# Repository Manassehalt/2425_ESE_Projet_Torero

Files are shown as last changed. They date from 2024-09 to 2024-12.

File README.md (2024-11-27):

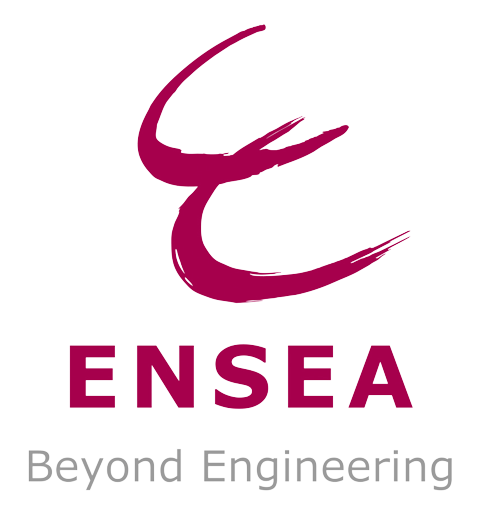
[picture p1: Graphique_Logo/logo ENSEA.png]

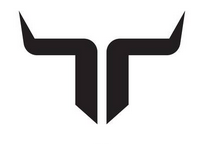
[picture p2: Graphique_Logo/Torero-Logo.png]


# 2425_ESE_Projet_Torero

## Projet de ESE de 3éme année de JACQUOT Nolan, GUIFFAULT Gabriel, BOULOT Paul et THOMAR Jean-Philippe

Ce projet contient toute les ressources de l'élaboration d'un robot capable de jouer au chat et a la souris.
Les liens vers les differentes ressources sont énuméré avec un court intitulé a la FIN du README.
Ci dessous le schéma architectural donnant les grandes lignes du projet.
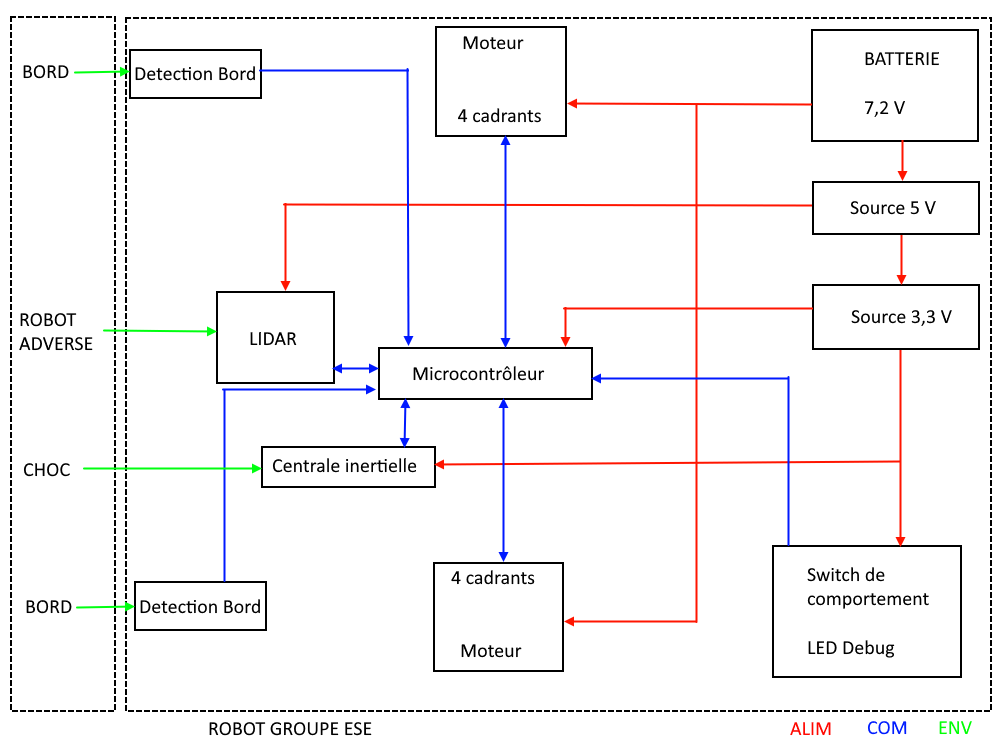
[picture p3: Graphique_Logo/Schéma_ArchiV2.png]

[Schéma architectural](https://github.com/user-attachments/files/17220902/Schema.architectural.pdf)

## Environnement:

> [!IMPORTANT]
> Table de 200cm x 160cm
> 
> Table sans Bord ni marquages!
> 
> Robot assimilable a un cylindre de 17 cm de diametre et 15 cm de hauteur 

## Cahier des charges:
> [!IMPORTANT]
>- Le robot doit etre capable de ce déplacer sur une table sans tomber (absence de bord et de marquage)
>- Le robot doit etre capable de detecter l'autre robot present sur la table pour le fuir ou le chasser en fonction de son role dans la partie.
>- Le robot doit etre capable de detecter un contact meme leger avec le robot adverse et changer son comportement d'un role vers l'autre.

Objectif annexe:
- Le robot peut realiser une odometrie simple pour suivre le bord de table lorsqu'il debute en souris
- Le robot peut realiser une odometrie simple pour se positionner au centre de la table avant de commencer la traque lorsqu'il debute en chat
- Le robot peut declencher un brusque changement de direction si il detecte un robot approchant rapidement en mode souris
- Le robot peut effectuer des prédiction de trajectoire et effectuer des trajectoires de collision en prévision du deplacement adverse en mode chat
- Le robot evite de prendre des directions ou il serait acculé dans un angle de table

### Dossier contenant les Datasheets : 
https://github.com/Manassehalt/2425_ESE_Projet_Torero/tree/main/Datasheet

### LISTE des choses faite ou a faire : 
https://github.com/Manassehalt/2425_ESE_Projet_Torero/blob/main/Calculs%20et%20brouillons/Remarque_Sch.md

### Lien utile : 
https://github.com/Manassehalt/2425_ESE_Projet_Torero/blob/main/Calculs%20et%20brouillons/Liens.xlsx

### BOM : 
https://github.com/Manassehalt/2425_ESE_Projet_Torero/blob/main/BOM.xlsx

### INFO PCB : 
https://github.com/Manassehalt/2425_ESE_Projet_Torero/blob/main/PCB/info_PCB.docx

### Apercu serigraphie :
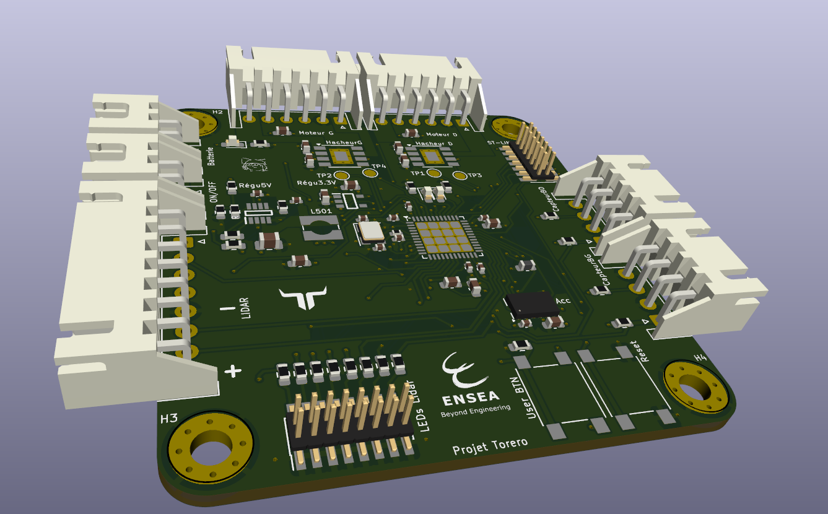
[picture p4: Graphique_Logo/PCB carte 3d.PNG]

[view PCB 3D](https://github.com/Manassehalt/2425_ESE_Projet_Torero/blob/main/Graphique_Logo/PCB%20carte%203d.PNG)

### DOSSIER PCB : 
https://github.com/Manassehalt/2425_ESE_Projet_Torero/tree/main/PCB

### Shematics_torero : 
https://github.com/Manassehalt/2425_ESE_Projet_Torero/blob/main/PCB/Projet_torero/Projet_torero.kicad_sch

### DOSSIER CODE STM32 : 
https://github.com/Manassehalt/2425_ESE_Projet_Torero/tree/main/Projet_ESE_STM32/Projet_ESE_Torero/STM32G431CBU6

### DOSSIER CALCULS : 
https://github.com/Manassehalt/2425_ESE_Projet_Torero/tree/8892ed05e16a1e8a040fe9dc08f9f57ab23dc9e8/Calculs%20et%20brouillons

### Methode si nouvel ordinateur : 
> [!TIP]
>Générer une clé SSH
>- Taper ssh-keygen puis Entrer
>- Appuyer sur y pour overwrite et sur Entrer pour passer les étapes (if no passphrase)
>- Taper cat ~/.ssh/id_ed25519.pub puis Entrer
>- Copier puis coller la clé dans GitHub Setting > SSH and GPG keys > SSH keys
>- Renommer avec le nom du PC pour savoir à quoi la clé correpond
>  ex : jeanp@HP-Pavilion-JP

### Ligne pour cloner un répertoire en utilisant le port 443 (https) au lieu du port 22, si bug sur la connexion:
> [!TIP]
>git clone ssh://git@ssh.github.com:443/username/Repositority_name.git

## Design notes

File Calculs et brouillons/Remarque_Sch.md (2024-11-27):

# !! LISTE A FAIRE !!
<details open>
<summary> <strong><ins>Schema:</ins></strong> </summary>
	
- [x] Regarder pour encodeurs 
- [x] Reprendre régulateur 5V (entrée à gauche et sortie à droite) 
- [x] VDDA pas alimenté 
- [x] Calculer valeur R pour les leds d'état 
- [x] supprimer label hiérarchique 7.2V 
- [x] Merge les feuilles pour moteur afin de modifier les deux à la fois 
- [x] faire symbole tof 
- [x] remplir valeur composants 
- [x] Renommer comme il faut pins de communication accélero 
- [x] Remplir le readme avec les schémas + calculs + présentation globale (ne pas avoir à aller chercher les fichiers à gauche à droite)
- [ ] Mettre texte descriptif pour définir connections
- [x] valeur R 2k3 plutôt que 2.3k  
- [x] valeur C 100n plutôt que 0.1µF  
- [x] Rendre l'ensemble plus clair (label et autre) 
</details>

<details >
<summary>  <strong><ins> PCB :</ins></strong> </summary>

- [x] PCB 54mm x 57mm
- [x] 4 trou de fixation a 4mm du bord Taille M3 
- [x] Remplacer l'empreinte de l'interrupteur pour le deporter hors du PCB 
- [x] condo proche 
- [x] reverifier empreinte condo imperial 
- [x] mettre port ldidar a coté de l'alimentation 5V
- [x] orientation serio j201 
- [x] en dernier les gpio pour le routage
- [x] router en premier les signaux rapides comme oscillateur, puis connecteur j201
- [x] plan de masse unique ideal
- [x] plan alim en 3,3V
- [x] changer empreinte grosse bobine 
- [x] 7.2V refaire connection (pas le meme tag) 
- [x] interrupteur a refaire empeinte plus petite 
- [x] refaire alim en suivant doc conseillé / 3 via 
- [x] Inverser pin driver moteur +zone de connexion plutot que piste 
- [x] rapprocher pastilles de ground et alim des vias associé 
- [x] aligner les composants 
- [x] Rapprocher la partie puissance (driver moteur) 
- [x] regarder plan pour retirer les antennes 
- [x] découplage 
- [x] plan sur grosse bobine 
- [x] agrandir piste gros courant 
  Routage :
- [x] Changement règle du CI -> diamètre mini via 0.45
		       -> diamètre mini anneaux 0.075
		       -> voir avec prof pour confirmer modifs (via copié depuis   correction fiack)
- [x] TESTER LES CONNECTIONS
      
</details open> 

<details >
<summary> <strong> <ins> MECANIQUE: </ins></strong></summary>

- [x] designer le parchoc qui porte les capteur de bord 
- [x] designer les support ajustable
- [ ] imprimer les pieces du robot

</details>
<details >
<summary>  <strong><ins> SOFTWARE: </ins></strong></summary>

- [ ] piloter les driver moteurs
- [ ] piloter le lidar
- [ ] recevoir les donnés du lidar et les interpréter
- [x] recevoir les donnés de l'accelerometre
- [ ] recevoir les donnés des capteurs de bords
- [ ] realiser les comportement en odometrie
- [ ] coder les comportement de fuite/evitement
- [ ] coder les comportement de chasse/collision
</details>

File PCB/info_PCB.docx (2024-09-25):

Batterie :

- Broche 1 = +
- Broche 2 = -

Switch à mettre sur un connecteur car PCB directement sous Lidar

57mm/54mm

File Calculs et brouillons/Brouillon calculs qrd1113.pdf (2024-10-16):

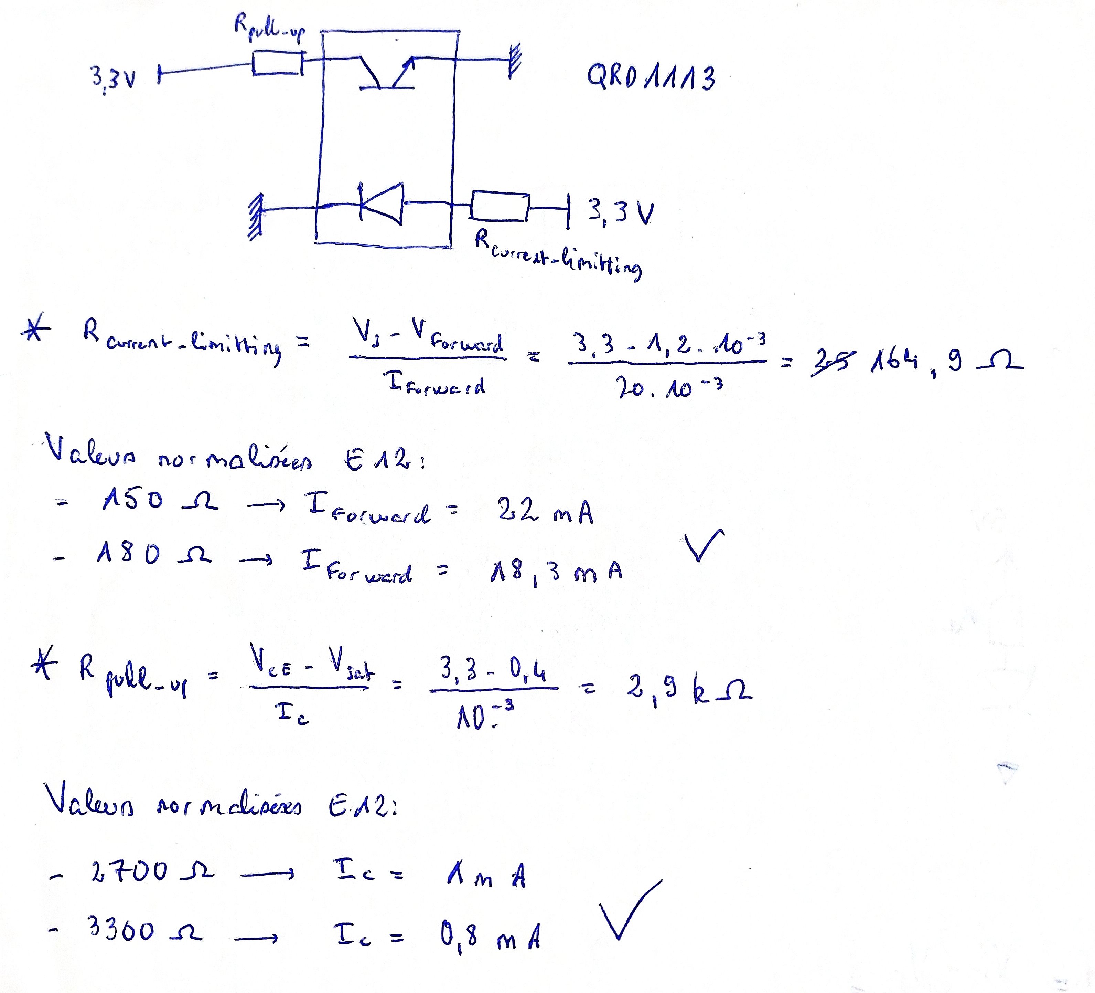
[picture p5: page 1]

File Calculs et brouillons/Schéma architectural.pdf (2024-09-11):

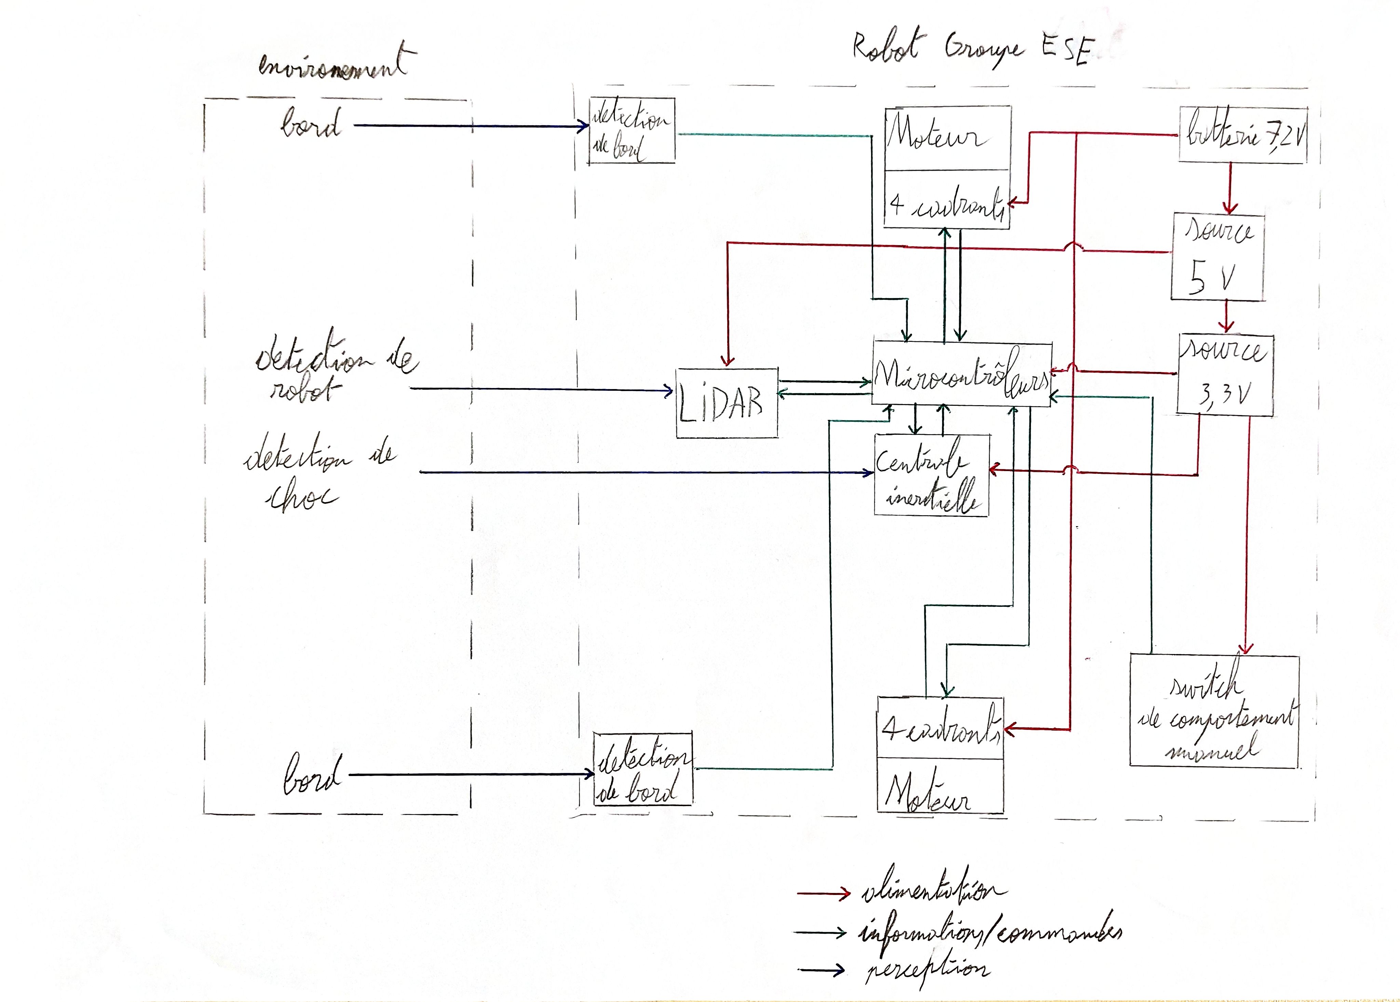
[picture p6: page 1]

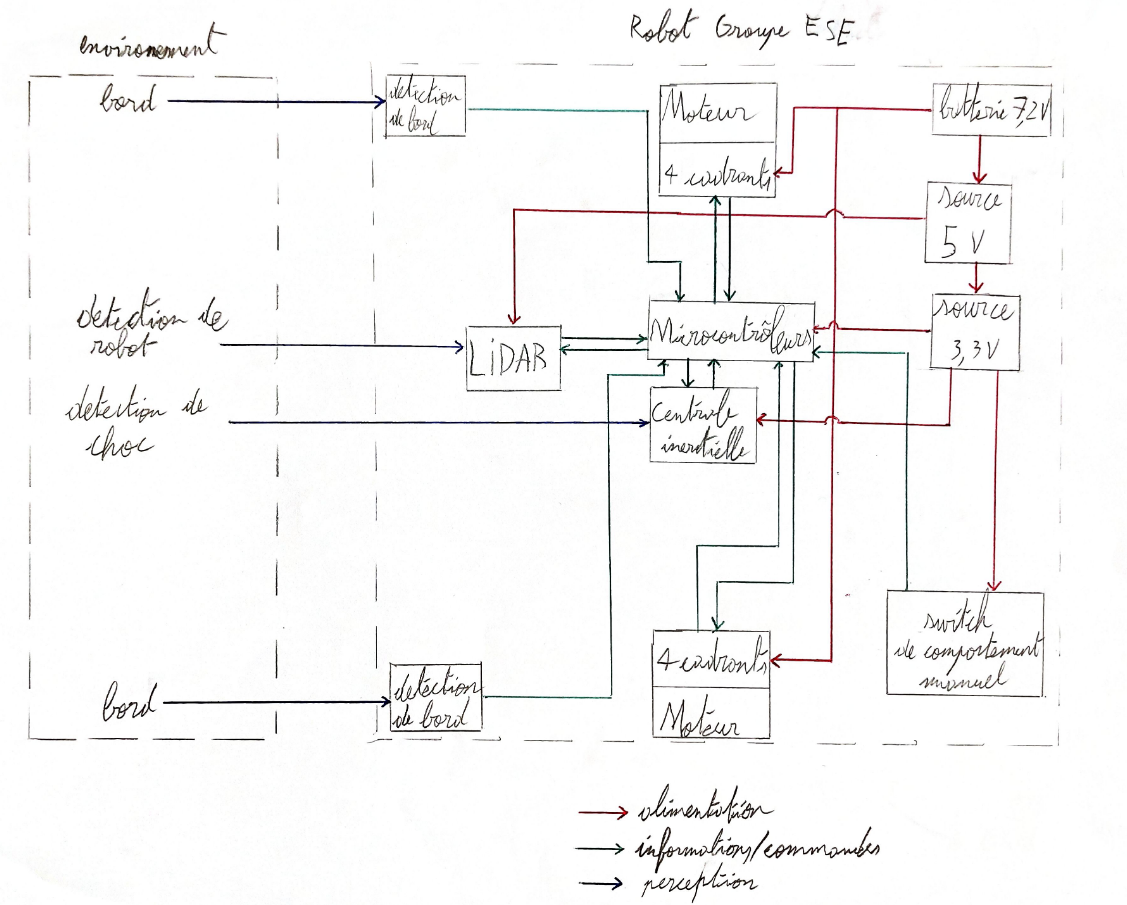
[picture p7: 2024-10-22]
Graphique_Logo/Schema_archi.png

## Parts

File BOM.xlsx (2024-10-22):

NOM | REFERENCE | FOURNISSEUR | DESCRIPTION | PRIX UNITAIRE | QUANTITE | COUT TOTAL | STATUS COMMANDE | DATASHEET
STM32G431CBU6 |  |  | Microcontrôleur |  | 1 | 0.00 €
Quartz 16 MHz | 2853935 | Farnell |  |  | 1 | 0.00 €
Connecteur SWD/STLink | 3226055 | Farnell |  |  |  | 0.00 €
ZXBM5210-SP-13 |  |  | Driver moteur |  |  | 0.00 €
DfRobot FIT0520 ou FIT0521 |  |  | Moteurs |  | 2 | 0.00 €
ADXL343BCCZ-RL |  |  | Accéléromètre |  | 1 | 0.00 €
MP1475S |  |  | Régulateur 5V |  | 1 | 0.00 €
BU33SD5WG-TR |  |  | Régulateur 3.3V |  | 1 | 0.00 €
NIMH 7.2V 1.3Ah (RS : 777-0377) |  |  | Batterie 7.2V |  |  | 0.00 €
QRD1113 | 1467857/1467858 | Farnell | Capteur bordure |  | 2 | 0.00 €
YDLIDAR X4 |  |  | Lidar |  | 1 | 0.00 €
Connecteurs JST 2.54mm |  |  |  |  |  | 0.00 €
LED + R/C |  |  |  |  |  | 0.00 € | en 0603
Résistance 10 k |  |  | Résistance boot flash user button |  | 1
Capacité 20p |  |  |  |  | 2
Capacité 100n |  |  |  |  | 8
Capacité 1u |  |  |  |  | 9
Capacité 4n7 |  |  |  |  | 1
Capacité 10n |  |  |  |  | 1
Capacité 22u |  |  |  |  | 1
Capacité 47u |  |  |  |  | 1
Capacité 10u |  |  |  |  | 2
Diode rouge |  |  |  |  | 2
Diode verte |  |  |  |  | 1
Connecteur Pin header 2x7 1,27mm ST Link |  |  |  |  | 1
Connecteur Pin header 2x8 1,27mm debug Lidar |  |  |  |  | 1
Connecteur JST 1x8 2,5mm Lidar |  |  |  |  | 1
Connecteurs JST 1x 2 2,5mm (batterie + switch) |  |  |  |  | 2
Connecteur JST 1x6 2,5mm moteur |  |  |  |  | 2
Inductance passe bas VDDA stm32 |  |  |  |  | 1
Inductance 4u7 |  |  | Régulateur tension 5V |  | 1
Résistance 10 |  |  |  |  | 1
Résistance 120 |  |  |  |  | 1
Résistance 140 |  |  |  |  | 2
Résistance 1k |  |  |  |  | 8
Résistance 100k |  |  |  |  | 2
Résistance 20 |  |  |  |  | 1
Résistance 16k |  |  |  |  | 1
Résistance 40k2 |  |  |  |  | 1
Résistance 7k68 |  |  |  |  | 1
Résistance 300 |  |  |  |  | 2
Résistance 15k3 |  |  |  |  | 2
Switch push |  |  | stm32 NRST et Boot Flash |  | 2

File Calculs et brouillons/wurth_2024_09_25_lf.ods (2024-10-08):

Value | Footprint | Tension | Qty | Wuerth
100nF | 402 | 25 | 1000 | 885012205085
15pF | 402 | 50 | 100 | 885012005056
10pF | 402 | 50 | 1000 | 885012005055
1uF | 603 | 25 | 1000 | 885012206076
10nF | 402 | 50 | 1000 | 885012205067
4.7uF | 603 | 10 | 1000 | 885012106012
22uF | 805 | 25 | 1000 | 885012107019
10uF | 603 | 25 | 1000 | 885012106031
6.8uH | >2A |  | 100 | 74404054068
4.7uH | >2A |  | 100 | 74404052047

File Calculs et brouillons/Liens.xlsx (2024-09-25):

DESCRIPTION | LIENS
Guide pour les calculs et branchement du capteur de bord QRD1113/14(attention arduino) | https://learn.sparkfun.com/tutorials/qrd1114-optical-detector-hookup-guide/all
Current Limiting Resistor: Protective Resistor for Regulating Current (for QRD1113/14) | https://www.ourpcb.com/current-limiting-resistor.html

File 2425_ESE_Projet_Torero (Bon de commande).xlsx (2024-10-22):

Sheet: Farnell
Farnell |  |  |  |  | Envoyez un seul fichier par mail!
Pos | I | P | Art | Désignation | Qté commandée | UA | Date Livraison | Prix unitaire | Devise | Q | Grpe | Div
10 | Z |  |  | 1467857 Capteur bordure QRD1113 | 4 | PC |  | 2.09 | EUR | PC | TA.01
20 | Z |  |  |  |  | PC |  |  | EUR | PC | TA.01
30 | Z |  |  |  |  | PC |  |  | EUR | PC | TA.01
40 | Z |  |  |  |  | PC |  |  | EUR | PC | TA.01
50 | Z |  |  |  |  | PC |  |  | EUR | PC | TA.01
60 | Z |  |  |  |  | PC |  |  | EUR | PC | TA.01
70 | Z |  |  |  |  | PC |  |  | EUR | PC | TA.01
80 | Z |  |  |  |  | PC |  |  | EUR | PC | TA.01
90 | Z |  |  |  |  | PC |  |  | EUR | PC | TA.01
100 | Z |  |  |  |  | PC |  |  | EUR | PC | TA.01
110 | Z |  |  |  |  | PC |  |  | EUR | PC | TA.01
120 | Z |  |  |  |  | PC |  |  | EUR | PC | TA.01
130 | Z |  |  |  |  | PC |  |  | EUR | PC | TA.01
140 | Z |  |  |  |  | PC |  |  | EUR | PC | TA.01
150 | Z |  |  |  |  | PC |  |  | EUR | PC | TA.01
160 | Z |  |  |  |  | PC |  |  | EUR | PC | TA.01
170 | Z |  |  |  |  | PC |  |  | EUR | PC | TA.01
180 | Z |  |  |  |  | PC |  |  | EUR | PC | TA.01
190 | Z |  |  |  |  | PC |  |  | EUR | PC | TA.01
MODE d'EMPLOI et CODE erreurs Version 19
1: indiquez le fournisseur ligne 1
2:remplissez pour chaque ligne commandée les 4 champs en rouge selon les règles suivantes:
 | Art
 |  |  | 2.1 | Ne mettez rien ici tout comme dans P: remplissez les zones rouges (et pas ailleurs)
 | Désignation
 |  |  | 2.2 | Ne dépassez pas les 40 caractères: il seront automatiquement effacés lors de la recopie
 |  |  | 2.3 | Mettre le code commande impérativement en premier suivi d'une courte description
 |  |  | 2.4 | Pour RS et Farnell : mettre le code commande RS ou Farnell (7 à 9 chiffres) (et pas la référence constructeur) suivie d'une courte description
 |  |  | 2.5 | Exemple: 125-4857 capa 1uF 0508
 | Qté commandée
 |  |  | 2.6 | C'est le nombre d'unités correspondant au prix unitaire
 |  |  | 2.7 | Attention il y a des pièges
 |  |  | 2.8 | avec RS par exemple on vous demande parfois de commander par lot de 5 par exemple
 |  |  | 2.9 | si vous commandez 1 lot : le nombre d'unité est alors 5 pour 1 lot et non 1
 | date
 |  |  | 2.10 | Pour la date: mettre la de date dans une semaine
 |  |  | 2.11 | La mettre au format JJ.MM.AAAA
 |  |  | 2.13 | Bien utiliser les points comme séparateur
 | prix unitaire
 |  |  | 2.14 | Le prix est le prix HT (sans la TVA 20%) en euros d'une unité | sauf pour les commandes au comptant ou chez un fournisseur étranger (EXP-TECH par exemple): mettez le prix TTC
 |  |  | 2.15 | arrondi au centime supérieur (0.012 euros devient 0.02!)
 |  |  | 2.16 | avec pour séparateur le point
 |  |  | 2.17 | n'utilisez pas le symbole euros d'excel
3: frais de port
 |  |  | 3.1 | ajoutez une ligne pour les frais de port
 |  |  | 3.2 | dont la désignation est "frais de port"
 |  |  | 3.3 | pas de frais de port à mettre pour RS ou Farnell
 |  |  | 3.4 | Renseignez vous pour connaître les frais de port | 9,9 euros TTC chez EXP par exemple
4: conseils complémentaires
 |  |  | 4.1 | Ne modifier que les 4 champs en rouge
 |  |  | 4.2 | Ne pas modifier le document sinon cela n'a plus aucun intérêt
 |  |  | 4.3 | Mettez les références dans le même ordre que celui de la commande
 |  |  | 4.4 | Vérifier bien sur les sites les références et les prix!
 |  |  | 4.5 | N'oubliez pas les frais de port!: ajoutez une ligne pour les mentionner
5: sauvegardez le fichier au format xls

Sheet: RS
RS |  |  |  |  | Envoyez un seul fichier par mail!
Pos | I | P | Art | Désignation | Qté commandée | UA | Date Livraison | Prix unitaire | Devise | Q | Grpe | Div
10 | Z |  |  | 820-1605 Connecteur JST 1x8 2,5mm | 5 | PC |  | 0.3 | EUR | PC | TA.01
20 | Z |  |  | 515-1349 connecteur JST 1x6 2,5mm | 10 | PC |  | 0.27 | EUR | PC | TA.01
30 | Z |  |  | 820-1582 connecteur JST 1x2 2,5mm | 5 | PC |  | 0.27 | EUR | PC | TA.01
40 | Z |  |  | 479-1435 switch push button 6 x 6 x 9.5mm | 20 | PC |  | 0.15 | EUR | PC | TA.01
50 | Z |  |  | 828-1866 connecteur pin header 2x8 1,27mm | 5 | PC |  | 2.05 | EUR | PC | TA.01
60 | Z |  |  | 828-1862 connecteur pin header 2x7 1,27mm | 5 | PC |  | 1.54 | EUR | PC | TA.01
70 | Z |  |  |  |  | PC |  |  | EUR | PC | TA.01
80 | Z |  |  |  |  | PC |  |  | EUR | PC | TA.01
90 | Z |  |  |  |  | PC |  |  | EUR | PC | TA.01
100 | Z |  |  |  |  | PC |  |  | EUR | PC | TA.01
110 | Z |  |  |  |  | PC |  |  | EUR | PC | TA.01
120 | Z |  |  |  |  | PC |  |  | EUR | PC | TA.01
130 | Z |  |  |  |  | PC |  |  | EUR | PC | TA.01
140 | Z |  |  |  |  | PC |  |  | EUR | PC | TA.01
150 | Z |  |  |  |  | PC |  |  | EUR | PC | TA.01
160 | Z |  |  |  |  | PC |  |  | EUR | PC | TA.01
170 | Z |  |  |  |  | PC |  |  | EUR | PC | TA.01
180 | Z |  |  |  |  | PC |  |  | EUR | PC | TA.01
190 | Z |  |  |  |  | PC |  |  | EUR | PC | TA.01
MODE d'EMPLOI et CODE erreurs Version 19
1: indiquez le fournisseur ligne 1
2:remplissez pour chaque ligne commandée les 4 champs en rouge selon les règles suivantes:
 | Art
 |  |  | 2.1 | Ne mettez rien ici tout comme dans P: remplissez les zones rouges (et pas ailleurs)
 | Désignation
 |  |  | 2.2 | Ne dépassez pas les 40 caractères: il seront automatiquement effacés lors de la recopie
 |  |  | 2.3 | Mettre le code commande impérativement en premier suivi d'une courte description
 |  |  | 2.4 | Pour RS et Farnell : mettre le code commande RS ou Farnell (7 à 9 chiffres) (et pas la référence constructeur) suivie d'une courte description
 |  |  | 2.5 | Exemple: 125-4857 capa 1uF 0508
 | Qté commandée
 |  |  | 2.6 | C'est le nombre d'unités correspondant au prix unitaire
 |  |  | 2.7 | Attention il y a des pièges
 |  |  | 2.8 | avec RS par exemple on vous demande parfois de commander par lot de 5 par exemple
 |  |  | 2.9 | si vous commandez 1 lot : le nombre d'unité est alors 5 pour 1 lot et non 1
 | date
 |  |  | 2.10 | Pour la date: mettre la de date dans une semaine
 |  |  | 2.11 | La mettre au format JJ.MM.AAAA
 |  |  | 2.13 | Bien utiliser les points comme séparateur
 | prix unitaire
 |  |  | 2.14 | Le prix est le prix HT (sans la TVA 20%) en euros d'une unité | sauf pour les commandes au comptant ou chez un fournisseur étranger (EXP-TECH par exemple): mettez le prix TTC
 |  |  | 2.15 | arrondi au centime supérieur (0.012 euros devient 0.02!)
 |  |  | 2.16 | avec pour séparateur le point
 |  |  | 2.17 | n'utilisez pas le symbole euros d'excel
3: frais de port
 |  |  | 3.1 | ajoutez une ligne pour les frais de port
 |  |  | 3.2 | dont la désignation est "frais de port"
 |  |  | 3.3 | pas de frais de port à mettre pour RS ou Farnell
 |  |  | 3.4 | Renseignez vous pour connaître les frais de port | 9,9 euros TTC chez EXP par exemple
4: conseils complémentaires
 |  |  | 4.1 | Ne modifier que les 4 champs en rouge
 |  |  | 4.2 | Ne pas modifier le document sinon cela n'a plus aucun intérêt
 |  |  | 4.3 | Mettez les références dans le même ordre que celui de la commande
 |  |  | 4.4 | Vérifier bien sur les sites les références et les prix!
 |  |  | 4.5 | N'oubliez pas les frais de port!: ajoutez une ligne pour les mentionner
5: sauvegardez le fichier au format xls

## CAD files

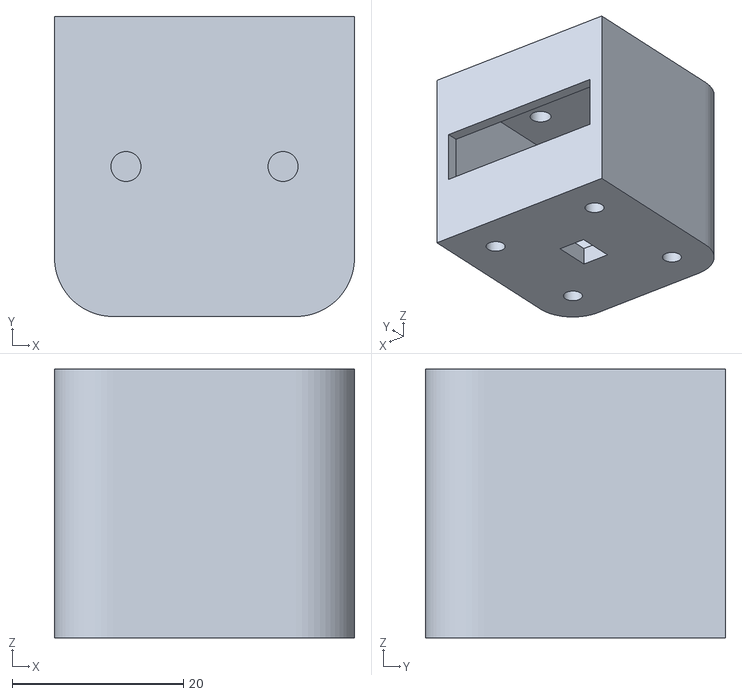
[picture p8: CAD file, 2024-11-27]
Meca/SupportCapteur.stl
35.0 x 35.0 x 31.4

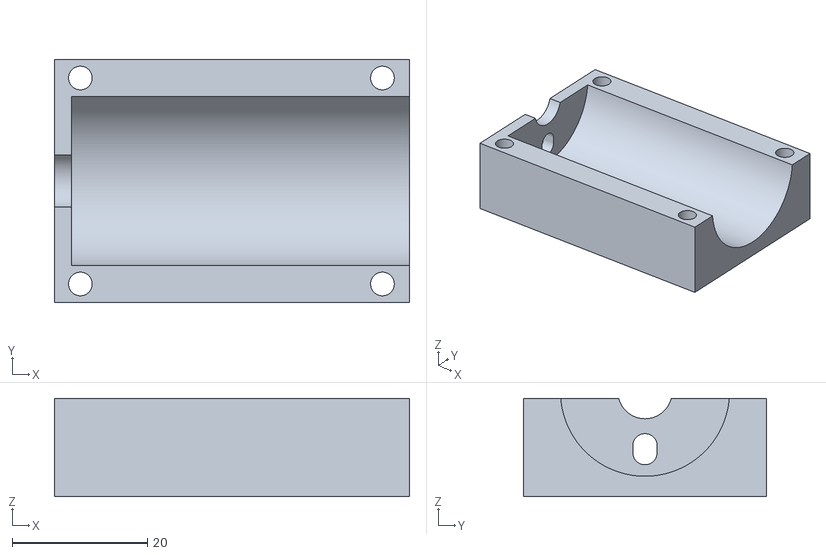
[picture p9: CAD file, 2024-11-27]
Meca/SupportMotor.stl
52.5 x 36.0 x 14.5

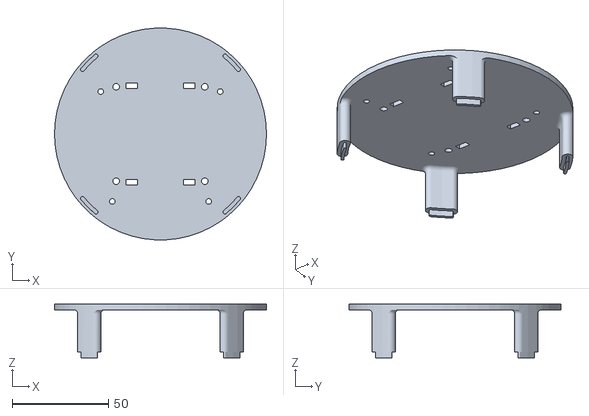
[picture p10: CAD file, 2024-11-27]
Meca/Tower.stl
110.0 x 109.8 x 28.0

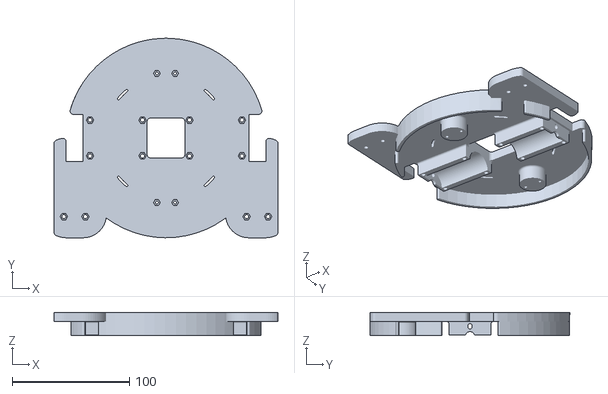
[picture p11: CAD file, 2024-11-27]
Meca/Base.stl
190.8 x 170.0 x 20.0

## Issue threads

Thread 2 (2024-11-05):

task list

gg-info, 2024-11-05:
# !! LISTE A FAIRE !!

- [x] Regarder pour encodeurs
- [x] Reprendre régulateur 5V (entrée à gauche et sortie à droite)
- [x] VDDA pas alimenté
- [x] Calculer valeur R pour les leds d'état
- [x] supprimer label hiérarchique 7.2V
- [x] Merge les feuilles pour moteur afin de modifier les deux à la fois
- [x] faire symbole tof
- [x] remplir valeur composants
- [x] Renommer comme il faut pins de communication accélero
- [x] Remplir le readme avec les schémas + calculs + présentation globale (ne pas avoir à aller chercher les fichiers à gauche à droite)
- [ ] Mettre texte descriptif pour définir connections
- [x] valeur R 2k3 plutôt que 2.3k
- [x] valeur C 100n plutôt que 0.1µF
- [x] Rendre l'ensemble plus clair (label et autre)

### Description du PCB :

- [x] PCB 54mm x 57mm
- [x] 4 trou de fixation a 4mm du bord Taille M3
- [x] Remplacer l'empreinte de l'interrupteur pour le deporter hors du PCB
- [x] condo proche
- [x] reverifier empreinte condo imperial
- [x] mettre port ldidar a coté de l'alimentation 5V
- [x] orientation serio j201
- [x] en dernier les gpio pour le routage
- [x] router en premier les signaux rapides comme oscillateur, puis connecteur j201
- [x] plan de masse unique ideal
- [x] plan alim en 3,3V
- [x] changer empreinte grosse bobine
- [x] 7.2V refaire connection (pas le meme tag)
- [x] interrupteur a refaire empeinte plus petite
- [x] refaire alim en suivant doc conseillé / 3 via
- [x] Inverser pin driver moteur +zone de connexion plutot que piste
- [x] rapprocher pastilles de ground et alim des vias associé
- [x] aligner les composants
- [x] Rapprocher la partie puissance (driver moteur)
- [x] regarder plan pour retirer les antennes
- [x] découplage
- [x] plan sur grosse bobine
- [x] agrandir piste gros courant
  Routage :
- [x] Changement règle du CI -> diamètre mini via 0.45
		       -> diamètre mini anneaux 0.075
		       -> voir avec prof pour confirmer modifs (via copié depuis   correction fiack)
- [ ] TESTER LES CONNECTIONS

### MECANIQUE:

- [ ] designer le parchoc qui porte les capteur de bord
- [ ] designer les support ajustable
- [ ] imprimer les pieces du robot

### SOFTWARE:

- [ ] piloter les driver moteurs
- [ ] piloter le lidar
- [ ] recevoir les donnés du lidar et les interpréter
- [ ] recevoir les donnés de l'accelerometre
- [ ] recevoir les donnés des capteurs de bords
- [ ] realiser les comportement en odometrie
- [ ] coder les comportement de fuite/evitement
- [ ] coder les comportement de chasse/collision

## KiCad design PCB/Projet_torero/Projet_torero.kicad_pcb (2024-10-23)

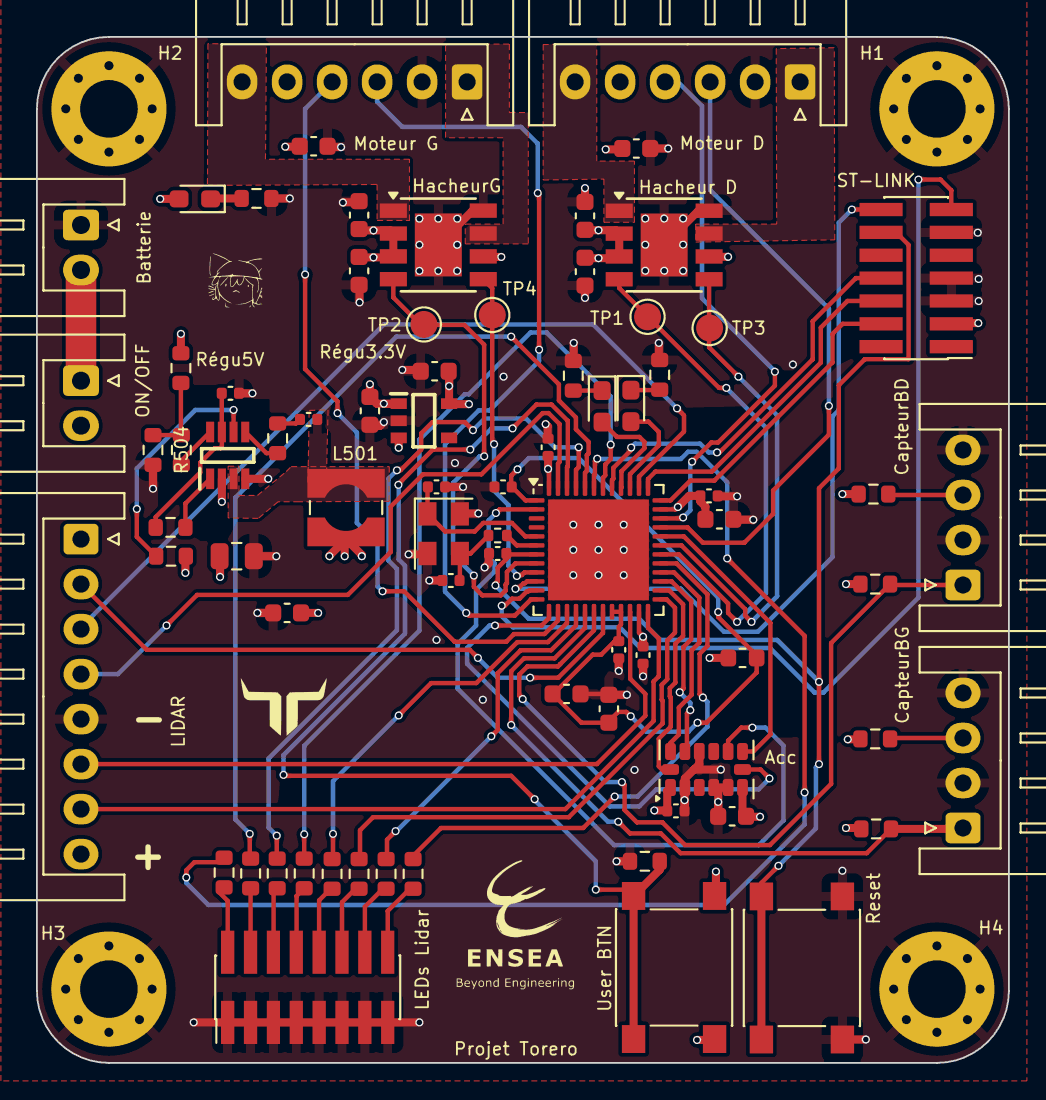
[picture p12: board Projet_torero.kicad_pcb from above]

Board: 4 copper layers, 54.0 x 57.0 mm, 79 parts (0 on the bottom side), 72 nets.

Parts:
10k201: 10k; R_0603_1608Metric
Acc: ADXL343; LGA-14_3x5mm_P0.8mm_LayoutBorder1x6y
Batterie: Conn_01x02; JST_XH_S2B-XH-A_1x02_P2.50mm_Horizontal
C201, C202: 20p; C_0402_1005Metric
C203, C204, C206, C207, C208, C402, C502, C503: 100n; C_0402_1005Metric
C205, C210, C401, C505, C506, C601, C603, C701, C703: 1u; C_0603_1608Metric
C209: 4n7; C_0603_1608Metric
C211: 10n; C_0402_1005Metric
C501: 22u; C_0805_2012Metric
C504: 47u; C_0603_1608Metric
C602, C702: 10u; C_0603_1608Metric
CapteurBD: JST_XH_S4B-XH-A_1x04_P2.50mm_Horizontal
CapteurBG: JST_XH_S4B-XH-A_1x04_P2.50mm_Horizontal
D1, D202: Red; LED_0603_1608Metric_Pad1.05x0.95mm_HandSolder
D201: Green; LED_0603_1608Metric_Pad1.05x0.95mm_HandSolder
H1, H2, H3, H4: MountingHole_Pad; MountingHole_3.2mm_M3_Pad_Via
Hacheur D: ZXBM5210-SP; Diodes_SO-8EP
HacheurG: ZXBM5210-SP; Diodes_SO-8EP
L202: L; L_0603_1608Metric
L501: 4u7; L_Wuerth_WE-TPC-3816
LEDs Lidar: Conn_02x08_Odd_Even; PinHeader_2x08_P1.27mm_Vertical_SMD
LIDAR: Conn_01x08; JST_XH_S8B-XH-A_1x08_P2.50mm_Horizontal
Moteur D: Conn_01x06; JST_XH_S6B-XH-A_1x06_P2.50mm_Horizontal
Moteur G: Conn_01x06; JST_XH_S6B-XH-A_1x06_P2.50mm_Horizontal
ON/OFF: Conn_01x02; JST_XH_S2B-XH-A_1x02_P2.50mm_Horizontal
R201: 10; R_0402_1005Metric
R202: 120; R_0603_1608Metric
R203, R314: 140; R_0603_1608Metric
R204, R205, R206, R207, R208, R209, R210, R211: 1k; R_0603_1608Metric
R501, R502: 100k; R_0603_1608Metric
R503: 20; R_0603_1608Metric
R504: 16k; R_0603_1608Metric
R505: 40k2; R_0603_1608Metric
R506: 7k68; R_0603_1608Metric
R801, R901: 300; R_0603_1608Metric
R802, R902: 15k3; R_0603_1608Metric
Reset: SW_Push; SW_Push_1P1T_NO_6x6mm_H9.5mm
Régu3.3V: BU33SD5WG-TR; SOT95P280X125-5N
Régu5V: MP1475SGJ-P; SOT65P280X100-8N
ST-LINK: Conn_02x07_Odd_Even; PinHeader_2x07_P1.27mm_Vertical_SMD
SW201: SW_Push; SW_Push_1P1T_NO_6x6mm_H9.5mm
TP1, TP2, TP3, TP4: TestPoint; TestPoint_Pad_D1.5mm
U201: STM32G431CBUx; QFN-48-1EP_7x7mm_P0.5mm_EP5.6x5.6mm
Y201: Crystal_GND24_Small; Crystal_SMD_EuroQuartz_MT-4Pin_3.2x2.5mm

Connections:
7.2V: C501.1, C601.2, C602.1, C701.2, C702.1, Hacheur D.2 (VM), Hacheur D.3 (VDD), Hacheur D.6 (VREF), HacheurG.2 (VM), HacheurG.3 (VDD), HacheurG.6 (VREF), ON/OFF.2, R501.1, Régu5V.2 (IN)
+3.3V: Acc.1 (Vdd_I/O), Acc.6 (Vs), C206.1, C207.1, C208.1, C209.1, C401.1, C402.2, C506.2, C603.2, C703.2, D201.2 (A), L202.1, Moteur D.5, Moteur G.5, R801.1, R802.2, R901.1, R902.2, Régu3.3V.5 (VOUT), ST-LINK.3, SW201.2, U201.23 (VDD), U201.35 (VDD), U201.48 (VDD)
+5V: C504.1, C505.1, L501.2, LIDAR.8, R505.1, Régu3.3V.1 (VIN), Régu3.3V.3 (STBY)
/ALIMENTATION/Sortie Régulateur 5V: C503.2, L501.1, Régu5V.3 (SW)
/CAPTEURS/ANALOG_OUTPUT_CAPT_BORD_D: CapteurBD.1, R901.2, U201.18 (PB1)
/CAPTEURS/ANALOG_OUTPUT_CAPT_BORD_G: CapteurBG.1, R801.2, U201.17 (PB0)
/CAPTEURS/CS_ACC: Acc.7 (~CS), U201.13 (PA5)
/CAPTEURS/DEV_EN_LIDAR: LIDAR.3, U201.38 (PA15)
/CAPTEURS/INT1_ACC: Acc.8 (INT1), U201.32 (PA10)
/CAPTEURS/INT2_ACC: Acc.9 (INT2), U201.2 (PC13)
/CAPTEURS/M_EN_LIDAR: LIDAR.2, U201.19 (PB2)
/CAPTEURS/M_SCTR_LIDAR: LIDAR.4, U201.47 (PB9)
/CAPTEURS/Rx_LIDAR: LIDAR.6, U201.22 (PB10)
/CAPTEURS/SCLK_ACC: Acc.14 (SCL/SCLK), U201.26 (PB13)
/CAPTEURS/SDI_ACC: Acc.13 (SDA/SDI/SDIO), U201.28 (PB15)
/CAPTEURS/SDO_ACC: Acc.12 (SDO/ADDR), U201.27 (PB14)
/CAPTEURS/Tx_LIDAR: LIDAR.7, U201.24 (PB11)
/PUISSANCE/EncodeurA_Droite: Moteur G.3, U201.12 (PA4)
/PUISSANCE/EncodeurA_Gauche: Moteur D.3, U201.33 (PA11)
/PUISSANCE/EncodeurB_Droite: Moteur G.4, U201.14 (PA6)
/PUISSANCE/EncodeurB_Gauche: Moteur D.4, U201.34 (PA12)
/PUISSANCE/FWDD: HacheurG.4 (FWD), TP2.1, U201.8 (PA0)
/PUISSANCE/FWDG: Hacheur D.4 (FWD), TP1.1, U201.30 (PA8)
/PUISSANCE/Moteur1/Commande moteur: HacheurG.7 (OUT2), Moteur G.1
/PUISSANCE/Moteur1/Connecteur Moteur: HacheurG.1 (OUT1), Moteur G.6
/PUISSANCE/Moteur/Commande moteur: Hacheur D.7 (OUT2), Moteur D.1
/PUISSANCE/Moteur/Connecteur Moteur: Hacheur D.1 (OUT1), Moteur D.6
/PUISSANCE/REVD: HacheurG.5 (REV), TP4.1, U201.9 (PA1)
/PUISSANCE/REVG: Hacheur D.5 (REV), TP3.1, U201.31 (PA9)
/STM32/USER_BTN: 10k201.2, SW201.1, U201.46 (PB8)
GND: 10k201.1, Acc.2 (GND), Acc.4 (GND), Acc.5 (GND), Acc.11 (RES), Batterie.1, C201.1, C202.2, C203.2, C204.2, C205.2, C206.2, C207.2, C208.2, C209.2, C210.2, C211.2, C401.2, C402.1, C501.2, C502.2, C504.2, C505.2, C506.1, C601.1, C602.2, C603.1, C701.1, C702.2, C703.1, CapteurBD.2, CapteurBD.4, CapteurBG.2, CapteurBG.4, H1.1, H2.1, H3.1, H4.1, Hacheur D.8 (GND), Hacheur D.9 (GND), HacheurG.8 (GND), HacheurG.9 (GND), LEDs Lidar.1, LEDs Lidar.3, LEDs Lidar.5, LEDs Lidar.7, LEDs Lidar.9, LEDs Lidar.11, LEDs Lidar.13, LEDs Lidar.15, LIDAR.5, Moteur D.2, Moteur G.2, R202.1, R203.1, R314.1, R506.2, Reset.1, Régu3.3V.2 (GND), Régu5V.4 (GND), ST-LINK.5, ST-LINK.7, ST-LINK.11, U201.49 (VSS), Y201.2, Y201.4
LED_E: R205.1, U201.44 (PB6)
LED_N: R204.1, U201.43 (PB5)
LED_NE: R208.1, U201.15 (PA7)
LED_NW: R209.1, U201.25 (PB12)
LED_S: R206.1, U201.45 (PB7)
LED_SE: R210.1, U201.16 (PC4)
LED_SW: R211.1, U201.29 (PC6)
LED_W: R207.1, U201.42 (PB4)
NRST: C203.1, Reset.2, ST-LINK.12, U201.7 (PG10)
unnamed: C201.2, R201.2, Y201.3
unnamed: C503.1, R503.1
unnamed: D1.1 (K), R314.2
unnamed: D201.1 (K), R202.2
unnamed: D202.1 (K), R203.2
unnamed: R503.2, Régu5V.5 (BST)
unnamed: R501.2, Régu5V.6 (EN/SYNC)
unnamed: R504.2, Régu5V.8 (FB)
unnamed: R502.2, Régu5V.1 (PG)
unnamed: C502.1, R502.1, Régu5V.7 (VCC)
unnamed: LEDs Lidar.2, R204.2
unnamed: LEDs Lidar.4, R205.2
unnamed: LEDs Lidar.6, R206.2
unnamed: LEDs Lidar.8, R207.2
unnamed: LEDs Lidar.10, R208.2
unnamed: LEDs Lidar.12, R209.2
unnamed: LEDs Lidar.14, R210.2
unnamed: LEDs Lidar.16, R211.2
unnamed: Batterie.2, ON/OFF.1
unnamed: CapteurBG.3, R802.1
unnamed: CapteurBD.3, R902.1
unnamed: R504.1, R505.2, R506.1
unnamed: C202.1, U201.5 (PF0), Y201.1
unnamed: R201.1, U201.6 (PF1)
unnamed: C204.1, C205.1, C210.1, C211.1, L202.2, U201.1 (VBAT), U201.20 (VREF+), U201.21 (VDDA)
STATUS_LED: D202.2 (A), U201.39 (PC10)
STATUS_LED_Debug: D1.2 (A), U201.40 (PC11)
SWCLK: ST-LINK.6, U201.37 (PA14)
SWDIO: ST-LINK.4, U201.36 (PA13)
SWO: ST-LINK.8, U201.41 (PB3)
VCP_RX: ST-LINK.13, U201.11 (PA3)
VCP_TX: ST-LINK.14, U201.10 (PA2)

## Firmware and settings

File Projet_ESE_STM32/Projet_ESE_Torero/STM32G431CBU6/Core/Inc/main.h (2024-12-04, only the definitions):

#define INT2_ACC_Pin GPIO_PIN_13
#define INT2_ACC_GPIO_Port GPIOC
#define RESET_Pin GPIO_PIN_10
#define RESET_GPIO_Port GPIOG
#define CS_ACC_Pin GPIO_PIN_5
#define CS_ACC_GPIO_Port GPIOA
#define LED_NE_Pin GPIO_PIN_7
#define LED_NE_GPIO_Port GPIOA
#define LED_SE_Pin GPIO_PIN_4
#define LED_SE_GPIO_Port GPIOC
#define ADC1_IN15_AN_CB_G_Pin GPIO_PIN_0
#define ADC1_IN15_AN_CB_G_GPIO_Port GPIOB
#define ADC1_IN12_AN_CB_D_Pin GPIO_PIN_1
#define ADC1_IN12_AN_CB_D_GPIO_Port GPIOB
#define M_EN_LIDAR_Pin GPIO_PIN_2
#define M_EN_LIDAR_GPIO_Port GPIOB
#define USART3_TX_LIDAR_Pin GPIO_PIN_10
#define USART3_TX_LIDAR_GPIO_Port GPIOB
#define USART3_RX_LIDAR_Pin GPIO_PIN_11
#define USART3_RX_LIDAR_GPIO_Port GPIOB
#define LED_NW_Pin GPIO_PIN_12
#define LED_NW_GPIO_Port GPIOB
#define SPI2_SCK_TO_SCLK_ACC_Pin GPIO_PIN_13
#define SPI2_SCK_TO_SCLK_ACC_GPIO_Port GPIOB
#define SPI2_MISO_TO_SDO_ACC_Pin GPIO_PIN_14
#define SPI2_MISO_TO_SDO_ACC_GPIO_Port GPIOB
#define SPI2_MOSI_TO_SDI_ACC_Pin GPIO_PIN_15
#define SPI2_MOSI_TO_SDI_ACC_GPIO_Port GPIOB
#define LED_SW_Pin GPIO_PIN_6
#define LED_SW_GPIO_Port GPIOC
#define INT1_ACC_Pin GPIO_PIN_10
#define INT1_ACC_GPIO_Port GPIOA
#define DEV_EN_LIDAR_Pin GPIO_PIN_15
#define DEV_EN_LIDAR_GPIO_Port GPIOA
#define Status_LED_Pin GPIO_PIN_10
#define Status_LED_GPIO_Port GPIOC
#define Status_LED_debbug_Pin GPIO_PIN_11
#define Status_LED_debbug_GPIO_Port GPIOC
#define LED_W_Pin GPIO_PIN_4
#define LED_W_GPIO_Port GPIOB
#define LED_N_Pin GPIO_PIN_5
#define LED_N_GPIO_Port GPIOB
#define LED_E_Pin GPIO_PIN_6
#define LED_E_GPIO_Port GPIOB
#define LED_S_Pin GPIO_PIN_7
#define LED_S_GPIO_Port GPIOB
#define BOOT_Flash_Pin GPIO_PIN_8
#define BOOT_Flash_GPIO_Port GPIOB
#define TIM4_CH4_M_SCTR_LIDAR_Pin GPIO_PIN_9
#define TIM4_CH4_M_SCTR_LIDAR_GPIO_Port GPIOB

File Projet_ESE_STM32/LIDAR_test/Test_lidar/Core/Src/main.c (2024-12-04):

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
/* Includes ------------------------------------------------------------------*/
#include "main.h"

/* USER CODE BEGIN Includes */
#include <stdio.h>
/* USER CODE END Includes */

/* USER CODE BEGIN PD */
#define DATA_SIZE_LIDAR 4000
#define START_CMD_LIDAR 0xA5
#define SCAN_CMD_LIDAR 0x60
#define GET_INFO_CMD_LIDAR 0x90
/* USER CODE END PD */

TIM_HandleTypeDef htim4;

UART_HandleTypeDef huart2;
UART_HandleTypeDef huart3;

/* USER CODE BEGIN PV */
uint8_t data_lidar[DATA_SIZE_LIDAR];

/* USER CODE END PV */

void SystemClock_Config(void);
static void MX_GPIO_Init(void);
static void MX_TIM4_Init(void);
static void MX_USART3_UART_Init(void);
static void MX_USART2_UART_Init(void);
/* USER CODE BEGIN 0 */
void lidar_Init(void){
	// Enable DEV_EN lidar
	HAL_GPIO_WritePin(GPIOA, LD2_Pin|DEV_EN_LIDAR_Pin, GPIO_PIN_SET);

	// Enable M_EN lidar
	HAL_GPIO_WritePin(M_EN_LIDAR_GPIO_Port, M_EN_LIDAR_Pin, GPIO_PIN_SET);
}

void get_lidar_data(){
	if(HAL_UART_Receive(&huart3, data_lidar, DATA_SIZE_LIDAR, (uint32_t) 1000)== HAL_OK){
		printf(" data lidar : %d\r\n", data_lidar[1]);
	}
	else{
		printf("Erreur de com lidar\r\n");
	}
}

int lidar_Start(){
	uint8_t lidar_command[2] = {START_CMD_LIDAR, SCAN_CMD_LIDAR};
	HAL_UART_Transmit(&huart3, lidar_command, 2, 2000);
	if(HAL_UART_Receive(&huart3, data_lidar, DATA_SIZE_LIDAR, 2000)==HAL_OK){
		for (int i = 0; i < 10; i++) {
//		    printf("Data lidar%d : %d\r\n", i + 1, data_lidar[i]);
		}
		return 1;
	}
	else{
//		printf("Erreur\r\n");
		return 0;
	}
}


/* USER CODE END 0 */

/**
  * @brief  The application entry point.
  * @retval int
  */
int main(void)
{

  /* MCU Configuration--------------------------------------------------------*/

  /* Reset of all peripherals, Initializes the Flash interface and the Systick. */
  HAL_Init();

  /* Configure the system clock */
  SystemClock_Config();

  /* Initialize all configured peripherals */
  MX_GPIO_Init();
  MX_TIM4_Init();
  MX_USART3_UART_Init();
  MX_USART2_UART_Init();
  /* USER CODE BEGIN 2 */
  lidar_Init();
//  printf("==============START==============\r\n");

  /* USER CODE END 2 */

  /* Infinite loop */
  /* USER CODE BEGIN WHILE */
  while (1)
  {
	  lidar_Start();
	  HAL_Delay(5000);
    /* USER CODE END WHILE */

    /* USER CODE BEGIN 3 */
  }
  /* USER CODE END 3 */
}

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


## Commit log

2024-09-11 BOM added
    [BOM.xlsx]
2024-09-11 Modif BOM
    [BOM.xlsx]
2024-09-11 Add Item Column
    [BOM.xlsx]
2024-09-11 Filling BOM file
    [BOM.xlsx]
2024-09-18 add kicad
    [CAPTEURS.kicad_sch, PUISSANCE.kicad_sch, Projet_torero.kicad_pcb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]
2024-09-18 kicad capteurs modif
    [BOM.xlsx, CAPTEURS.kicad_sch, PUISSANCE.kicad_sch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]
2024-09-18 modif capteurs
    [CAPTEURS.kicad_sch]
2024-09-25 Ajout info PCB 25/09
2024-09-25 Rajouté la STM32
    [STM32.kicad_sch]
2024-09-25 add kicad puissance
    [PUISSANCE.kicad_sch]
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2024-09-25 modif kicad capteur + excel liens/sources
    [CAPTEURS.kicad_sch, Liens.xlsx]
2024-10-01 Mis à jour, manque l'interupteur ON/OFF
    [Alimentation.kicad_sch, Projet_torero.kicad_sch]
2024-10-01 Inversion pins lidar
    [CAPTEURS.kicad_sch]
2024-10-01 Rajout interupteur ON/OFF
    [Alimentation.kicad_sch]
2024-10-01 Corriger les erreurs de la STM
    [STM32.kicad_sch]
2024-10-01 modification moteurs et alim
    [Alimentation.kicad_sch, Moteur.kicad_sch, PUISSANCE.kicad_sch]
2024-10-01 modif capa moteur
    [Moteur.kicad_sch]
2024-10-01 modif alim
    [Alimentation.kicad_sch]
2024-10-01 modif alim fin ?
    [Alimentation.kicad_sch]
2024-10-01 modif valeur composants passifs
    [Alimentation.kicad_sch, STM32.kicad_sch]
2024-10-02 Mit à jour les encodeurs
    [PUISSANCE.kicad_sch, STM32.kicad_sch]
2024-10-02 modif labels hiérarchiques
    [Projet_torero.kicad_sch]
2024-10-02 Update README.md
    Rajout de lien et une courte introduction
2024-10-02 add symbole capteur de bord
2024-10-02 Update README.md
    rajout des datasheets
2024-10-02 ajout nouvelles feuilles capteurs bords
    [CAPTEURS.kicad_sch, Projet_torero.kicad_sch, capteur_bord_2.kicad_sch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]
2024-10-02 ajout modif capteurs de bord
    [CAPTEURS.kicad_sch, capteur_bord_2.kicad_sch, carpteur_bord_1.kicad_sch]
2024-10-02 ajout valeur capa accelerometer
    [CAPTEURS.kicad_sch]
2024-10-02 Update README.md
    rajout de mise en page/hierarchie
2024-10-02 modif capteur
    [CAPTEURS.kicad_sch, STM32.kicad_sch, capteur_bord_2.kicad_sch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]
2024-10-02 review sch
    [Alimentation.kicad_sch, CAPTEURS.kicad_sch, Projet_torero.kicad_sch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]
2024-10-02 review sch 2
    [STM32.kicad_sch]
2024-10-02 review sch après vérif prof
    [Alimentation.kicad_sch, CAPTEURS.kicad_sch, Capteur_Bord.kicad_sch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]
2024-10-02 changement pins STlink
    [Capteur_Bord.kicad_sch, STM32.kicad_sch]
2024-10-02 Update README.md
    Cahier des charges
2024-10-02 changement schéma
    [Alimentation.kicad_sch, CAPTEURS.kicad_sch, Capteur_Bord.kicad_sch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]
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2024-10-08 Librairies
    Ajoute des librairies de composants
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2024-10-08 Liste empreintes
    passive R and C
    [wurth_2024_09_25_lf.ods]
2024-10-08 Ajout capteur bordure
    [BOM.xlsx]
2024-10-08 modif capteur de bord
    [Capteur_Bord.kicad_sch]
2024-10-08 maj pin STM
    [Capteur_Bord.kicad_sch, STM32.kicad_sch]
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2024-10-08 Re-Push pour les empreintes et le PCB
    [Projet_torero.kicad_pcb, STM32.kicad_sch]
2024-10-08 modif placement composant
    [Alimentation.kicad_sch, CAPTEURS.kicad_sch, Capteur_Bord.kicad_sch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]
2024-10-09 Update README.md
    Rajout des dossier software
2024-10-09 Refait l'alimentation
    [Alimentation.kicad_sch]
2024-10-09 modif routing
    [Projet_torero.kicad_pcb]
2024-10-09 Mis à jour des composants
    [Alimentation.kicad_sch, STM32.kicad_sch]
2024-10-09 Ajout Switch ON/OFF sur carte
    [Alimentation.kicad_sch, Capteur_Bord.kicad_sch, Moteur.kicad_sch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]
2024-10-09 Nouvelle version avec Empreinte correcte
    [Alimentation.kicad_sch, Projet_torero.kicad_pcb, STM32.kicad_sch]
2024-10-09 Placement des composants
    [Capteur_Bord.kicad_sch, Projet_torero.kicad_pcb]
2024-10-09 rangement dossiers
    [Liens.xlsx, wurth_2024_09_25_lf.ods]
2024-10-09 Correction Prof
    [Alimentation.kicad_sch, CAPTEURS.kicad_sch, Capteur_Bord.kicad_sch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]
2024-10-09 Placement des composant "terminé"
    [Alimentation.kicad_sch, Moteur.kicad_sch, Projet_torero.kicad_pcb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]
2024-10-09 changement pin usart2
    [Projet_torero.kicad_pcb, STM32.kicad_sch]
2024-10-09 rectification erreur pin usart2
    [Projet_torero.kicad_pcb, STM32.kicad_sch]
2024-10-14 routage à valider
    [Projet_torero.kicad_pcb]
2024-10-16 Corriger les erreurs
    [Alimentation.kicad_sch, CAPTEURS.kicad_sch, Capteur_Bord.kicad_sch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]
2024-10-16 changement calculs capteur bord + modif bom
    [BOM.xlsx]
2024-10-16 Correction du PCB pour prof
    [Capteur_Bord.kicad_sch, Moteur.kicad_sch, Projet_torero.kicad_pcb]
2024-10-16 Correction suggestion prof
    [Alimentation.kicad_sch, Capteur_Bord.kicad_sch, Moteur.kicad_sch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]
2024-10-22 Modif BOM + ajout du bon de commande
    [2425_ESE_Projet_Torero (Bon de commande).xlsx, BOM.xlsx]
2024-10-22 Confirmation PCB
    Il manque juste a finir le texte et mettre les logos de l'ENSEA et du groupe TORERO
    [Moteur.kicad_sch, Projet_torero.kicad_pcb]
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2024-10-22 fichier gerber et ajout logo ensea
    [Projet_torero-B_Cu.gbl, Projet_torero-B_Mask.gbs, Projet_torero-B_Silkscreen.gbo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]
2024-10-23 ajout cornes taureau
    [Projet_torero-B_Cu.gbl, Projet_torero-B_Mask.gbs, Projet_torero-B_Silkscreen.gbo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]
2024-10-23 Update README.md
    j'ai fix les image du read me
2024-10-23 Ajoute du Gerber pour la fabrication
    [Projet_torero-B_Cu.gbl, Projet_torero-B_Mask.gbs, Projet_torero-B_Silkscreen.gbo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]
2024-10-23 Corrige petite erreur texte
    [Projet_torero.kicad_pcb]
2024-10-23 Changer le Gerber
    [Projet_torero-B_Cu.gbl, Projet_torero-B_Mask.gbs, Projet_torero-B_Silkscreen.gbo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]
2024-10-23 add projet stm pour test lidar
2024-10-23 Adapté la taille des pastilles
    [Projet_torero-B_Cu.gbl, Projet_torero-B_Mask.gbs, Projet_torero-B_Silkscreen.gbo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]
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2024-11-27 fichier meca
    [Base.stl, SupportCapteur.stl, SupportMotor.stl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]
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

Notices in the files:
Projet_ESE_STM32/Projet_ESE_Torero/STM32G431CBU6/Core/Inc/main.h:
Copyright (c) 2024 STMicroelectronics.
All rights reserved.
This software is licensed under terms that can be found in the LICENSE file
